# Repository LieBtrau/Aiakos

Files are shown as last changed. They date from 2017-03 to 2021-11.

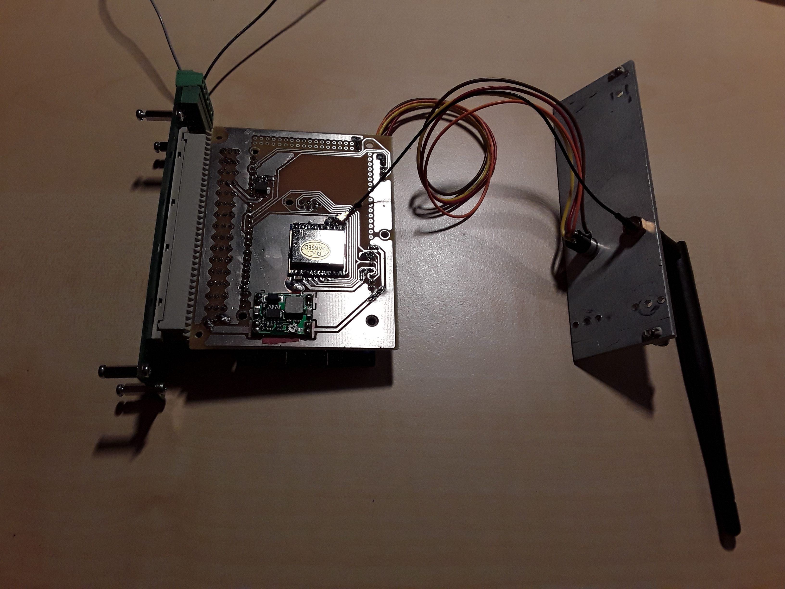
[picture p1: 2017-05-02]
Documentation/Pictures/20170501_215125.jpg

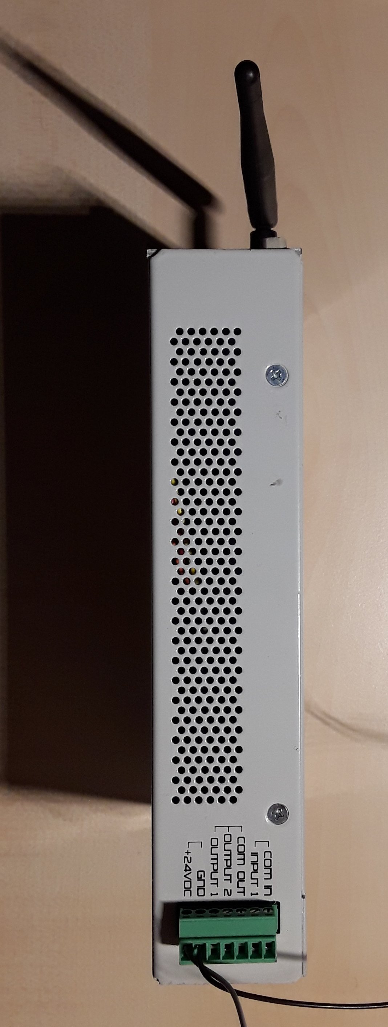
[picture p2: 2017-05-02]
Documentation/Pictures/20170501_215628.jpg

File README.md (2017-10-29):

# This project will solve the following problem
When arriving at home  with my bike, I find the garage door still locked.  I have to stop in front of the closed door, take of my backpack, find the keyfob and activate it.  It takes a few seconds then before the door is fully open and I can enter.  When it's raining heavily, every second outside is a second too much.

# Wish
While riding and coming near to my house, press a button on my bike so that the door opens.  By the time I arrive at the door, it's fully open and I can ride in the garage without having to stop on the drive way.

# Solution
The system will consist of three parts:  

* door controller in the garage  
* BLE-enabled key fob in my back pack  
* Wake up initializer  

## Door controller in the garage
The [door controller](https://github.com/LieBtrau/Aiakos/wiki/Garage-controller) is mounted in the garage and connected to the electric motor that can open and close the door.  With its [LoRa](https://www.lora-alliance.org/) module the controller can securely communicate to the key fob.  To make the system operational, the key fob must be paired with the door controller.  The pairing is done by connecting the door controller to the key fob with an audio-jack cable and pressing the button on the key fob.  The serial connection prevents man-in-the-middle (MITM) attacks.  To prevent eavesdropping, the serial connection is secured using [ECDH](https://en.wikipedia.org/wiki/Elliptic-curve_Diffie%E2%80%93Hellman).

## Key fob 
The [key fob](https://github.com/LieBtrau/Aiakos/wiki/Key-fob) is the access token to the system and should be kept safely by the user.  The key fob's Lora module enables communication to the door controller.  The key fob will be asleep most of the time.  When it receives a valid awake command, it will instruct the door controller to open/close the garage door.  The user can wake the key fob in two ways: either by pushing the key fob button, or by pushing the button on the wake up initializer.  
The key fob incorporates a [Bluetooth Low Energy](https://en.wikipedia.org/wiki/Bluetooth_Low_Energy) module to communicate with the wake up initializer.  The key fob will only allow a paired initializer to wake it up.  Pairing involves connecting the fob to the initializer using an audio jack cable and pressing the key fob button.

## Wake up initializer

# Alternatives
## Smartphone and garage controller with WiFi
An off-the-shelf bluetooth tracker is attached to the bike.  The user has a smartphone with a wireless data connection and bluetooth low energy support.  The garage is equipped with an internet connected controller.  After binding the tracker with the smartphone, the system is ready to use.  
Pressing the button on the bluetooth tracker, wakes up the service running on the smartphone.  The smartphone uses geo-location service to check if the smartphone is in the neighbourhood of the garage.  If so, then a command is sent through WiFi to instruct the garage controller to open the door.  
## Smartphone and garage controller with WiFi
The garage controller can be equipped with a bluetooth low energy peripheral IC.  The user could then operate the door using an application on a smartphone.  

*

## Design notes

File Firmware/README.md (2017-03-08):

#This project will solve the following problem
When arriving at home  with my bike, I find the garage door still locked.  I have to stop in front of the closed door, take of my backpack, find the keyfob and activate it.  It takes a few seconds then before the door is fully open and I can enter.  When it's raining heavily, every second outside is a second too much.

#Wish
While riding and coming near to my house, press a button on my bike so that the door opens.  By the time I arrive at the door, it's fully open and I can ride in the garage without having to stop on the drive way.

#Proposed solutions
##Not implemented: Using smartphone
An off-the-shelf bluetooth tracker is attached to the bike.  The user has a smartphone with a wireless data connection and bluetooth low energy support.  The garage is equipped with an internet connected controller.  After binding the tracker with the smartphone, the system is ready to use.  
Pressing the button on the bluetooth tracker, wakes up the service running on the smartphone.  The smartphone uses geo-location service to check if the smartphone is in the neighbourhood of the garage.  If so, then a command is sent through the cloud to instruct the garage controller to open the door.  

##Without smartphone
The system will consist of three parts:  

* door controller in the garage  
* Wake up initializer
* NFC-enabled key fob in my back pack  

###Door controller in the garage
The door controller in the garage is connected to the motor that can open and close the gate.  It will only do this when an authenticated request from a paired keyfob has been received by its wireless UHF-receiver.
During system setup, the key fob will have to be securely bound to the garage controller.  For ease of use, compliance with future addon, and prevention of man-in-the-middle (MITM) attacks, serial communication will be used.  The user will use a button to put the door controller in learn mode.  To pair the keyfob, the user connects keyfob and the controller with an audio jack cable and that's it.  Audio jack cables and connectors are cheaper and less power hungry than NFC readers and tags.

###Wake up initializer

###Key fob
After the key fob has been paired with the controller in the garage it will return to a low power sleep mode.  Reception of the correct code on the LF-receiver will wake up the key fob.  The UHF-transmitter in the key fob will then automatically send a request to the garage controller to open the gate.

###Used technologies
* 434MHz LoRa wireless communication
* Bluetooth Low Energy
* ...

#Future addon
The garage controller can be equipped with a bluetooth low energy peripheral IC.  The user could then operate the door using an application on a smartphone.  

* [Garage controller](../../wiki/Master:-garage-controller)

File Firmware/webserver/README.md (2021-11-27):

# What is this all about?
It's an ESP32 running a webserver.  Once you typed in the correct pincode on the ESP32's webpage, a GPIO will be toggled, which will open the garagedoor.
## Security
3 layer security:

 1. The ESP32 only exists as a local device on the Wifi-network.  It's behind the firewall, so it can't be accessed from the internet.  You'll need to know the WiFi-password first.
 2. IP-traffic to the ESP32 is encrypted by TLS1.2, using a self-signed certificate
 3. The user must know the correct pin code.
## Implementation
The code is written in Micropython/CircuitPython.  The source files can be found in this repository.  To make it all work, you'll need to generate your own configuration files.  Examples of these two files follow:
### config.json
    {
	    "secure-connection": "true",
	    "hostname": "esp32_wifi",
	    "secure-tcp-port": "443",
	    "unsecure-tcp-port": "80",
	    "ip-address": "192.168.1.254",
	    "netmask": "255.255.255.0",
	    "default-route": "192.168.1.1",
	    "dns": "8.8.8.8",
	    "pincodes": [
	        "1234",
	        "4321"
	    ]
	}
### wifi-credentials.json
    {
    "SSID" : "MyWifiSSID",
    "PASS" : "MySecretWiFiPassword"
	}

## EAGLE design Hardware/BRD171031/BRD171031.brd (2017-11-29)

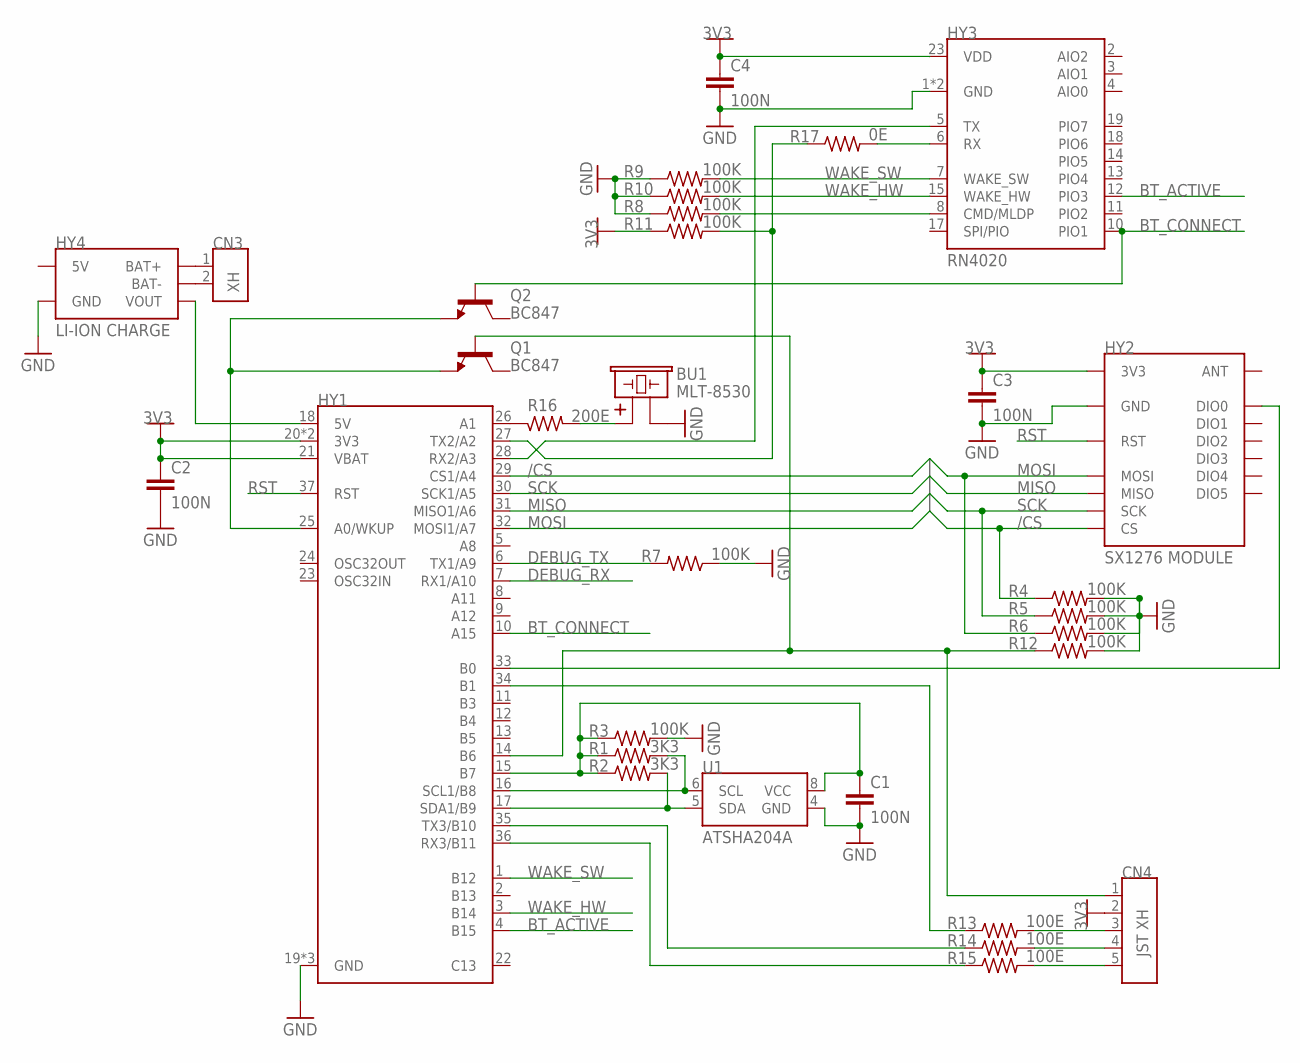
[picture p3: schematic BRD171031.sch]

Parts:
BU1: MLT-8530; BU_8530
C1, C2, C3, C4: 100N; CA_1206
CN3: XH; CN_HDR_1X2_180D_P25_JST_B2B-XH
CN4: JST XH; CN_HDR_1X5_180D_P25_JST_B5B-XH
HY1: HY_DEVBRD_BLUEPILL; HY_DEVBRD_BLUEPILL_SMD
HY2: SX1276 MODULE; HY_SX1276
HY3: RN4020; HY_BLE_RN4020
HY4: LI-ION CHARGE; HY_PMMOD_LIION
Q1, Q2: BC847; SC_SOT23
R1, R2: 3K3; RE_1206
R3, R4, R5, R6, R7, R8, R9, R10, R11, R12: 100K; RE_1206
R13, R14, R15: 100E; RE_1206
R16: 200E; RE_1206
R17: 0E; RE_1206
U1: ATSHA204A; SC_SO08

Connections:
3V3: C2.1, C3.1, C4.1, CN4.2, HY1.20 (3V3), HY1.21 (VBAT), HY1.38 (3V3), HY2.VCC (3V3), HY3.23 (VDD), R11.1
/CS: HY1.29 (CS1/A4), HY2.NSS (CS), R4.1
BTN: CN4.1, HY1.14 (B6), Q1.1 (B), R12.1
BT_ACTIVE: HY1.4 (B15), HY3.12 (PIO3)
BT_CONNECT: HY1.10 (A15), HY3.10 (PIO1), Q2.1 (B)
DEBUG_RX: HY1.7 (RX1/A10)
DEBUG_TX: HY1.6 (TX1/A9), R7.2
GND: BU1.2, C1.2, C2.2, C3.2, C4.2, HY1.19 (GND), HY1.39 (GND), HY1.40 (GND), HY2.GND, HY2.GND@1 (GND), HY2.GND@2 (GND), HY3.1 (GND), HY3.24 (GND), HY4.GND1 (GND), HY4.GND2 (GND), R3.2, R4.2, R5.2, R6.2, R7.1, R8.1, R9.1, R10.1, R12.2, U1.4 (GND)
MISO: HY1.31 (MISO1/A6), HY2.MISO
MOSI: HY1.32 (MOSI1/A7), HY2.MOSI, R6.1
unnamed: HY3.6 (RX), R17.2
unnamed: HY1.33 (B0), HY2.DIO0
unnamed: HY1.27 (TX2/A2), R11.2, R17.1
unnamed: HY1.28 (RX2/A3), HY3.5 (TX)
unnamed: HY3.8 (CMD/MLDP), R8.2
unnamed: HY1.36 (RX3/B11), R15.1
unnamed: HY1.35 (TX3/B10), R14.1
unnamed: HY1.34 (B1), R13.1
unnamed: HY1.25 (A0/WKUP), Q1.2 (E), Q2.2 (E)
unnamed: HY1.26 (A1), R16.1
unnamed: CN4.3, R13.2
unnamed: CN4.4, R14.2
unnamed: CN4.5, R15.2
unnamed: BU1.1, R16.2
unnamed: HY1.18 (5V), HY4.OUT+ (VOUT)
unnamed: CN3.1, HY4.B+ (BAT+)
unnamed: CN3.2, HY4.B- (BAT-)
PWR_U1: C1.1, HY1.15 (B7), R1.1, R2.1, R3.1, U1.8 (VCC)
RST: HY1.37 (RST), HY2.REST (RST)
SCK: HY1.30 (SCK1/A5), HY2.SCK, R5.1
SCL: HY1.16 (SCL1/B8), R1.2, U1.6 (SCL)
SDA: HY1.17 (SDA1/B9), R2.2, U1.5 (SDA)
WAKE_HW: HY1.3 (B14), HY3.15 (WAKE_HW), R10.2
WAKE_SW: HY1.1 (B12), HY3.7 (WAKE_SW), R9.2

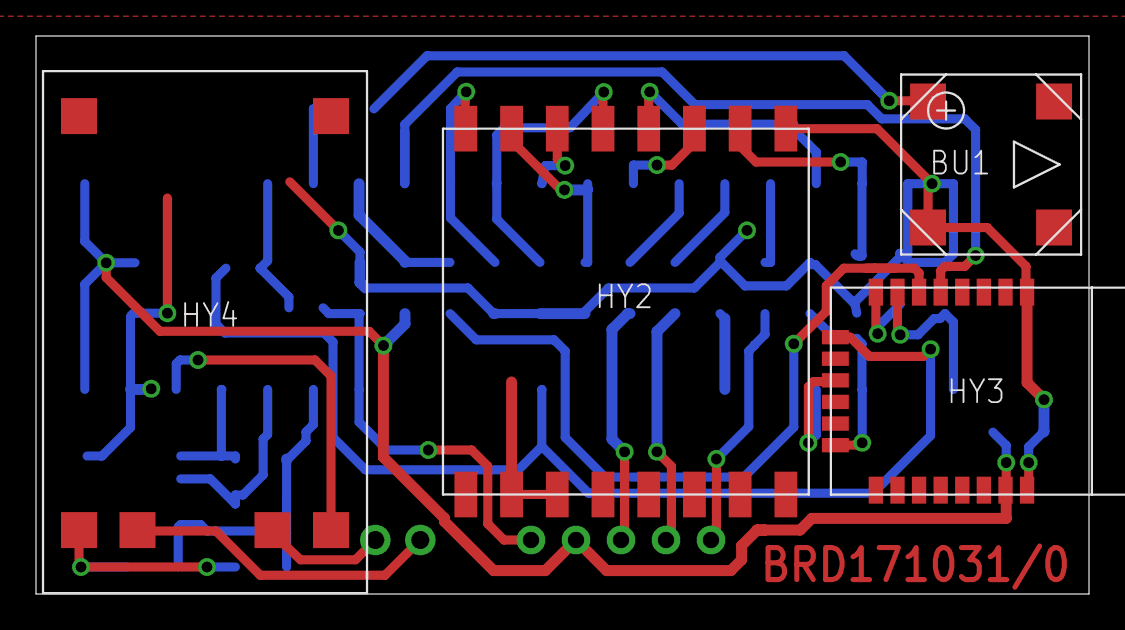
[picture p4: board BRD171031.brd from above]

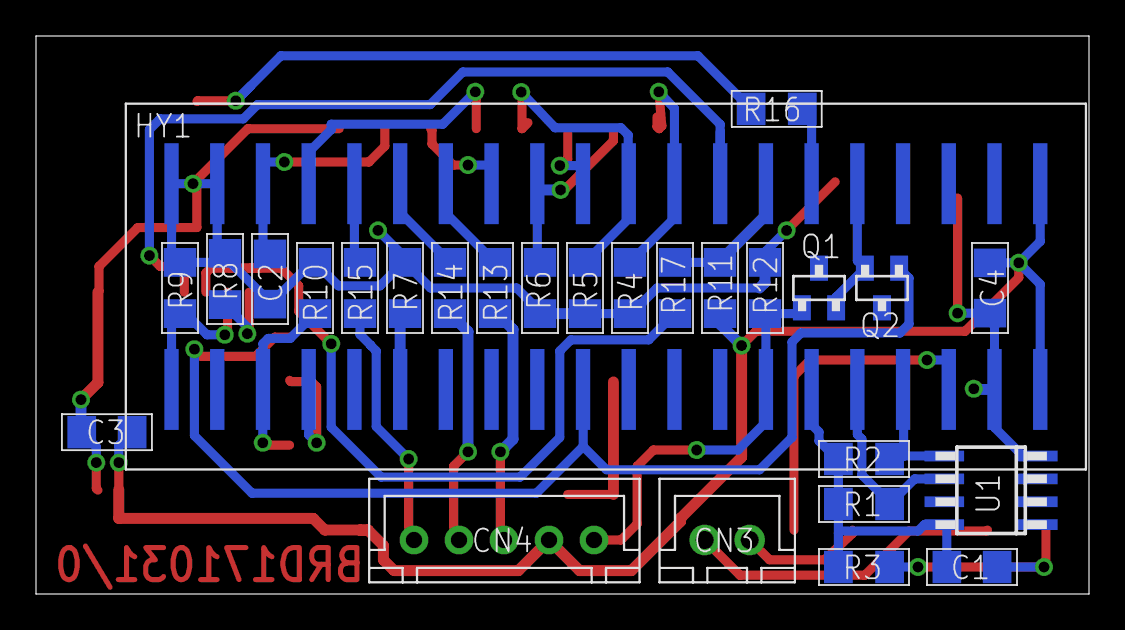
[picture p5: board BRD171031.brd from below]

Board: 2 copper layers, 58.5 x 31.0 mm, 32 parts (27 on the bottom side), 33 nets.

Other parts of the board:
U$2: MC_FRAME_A5

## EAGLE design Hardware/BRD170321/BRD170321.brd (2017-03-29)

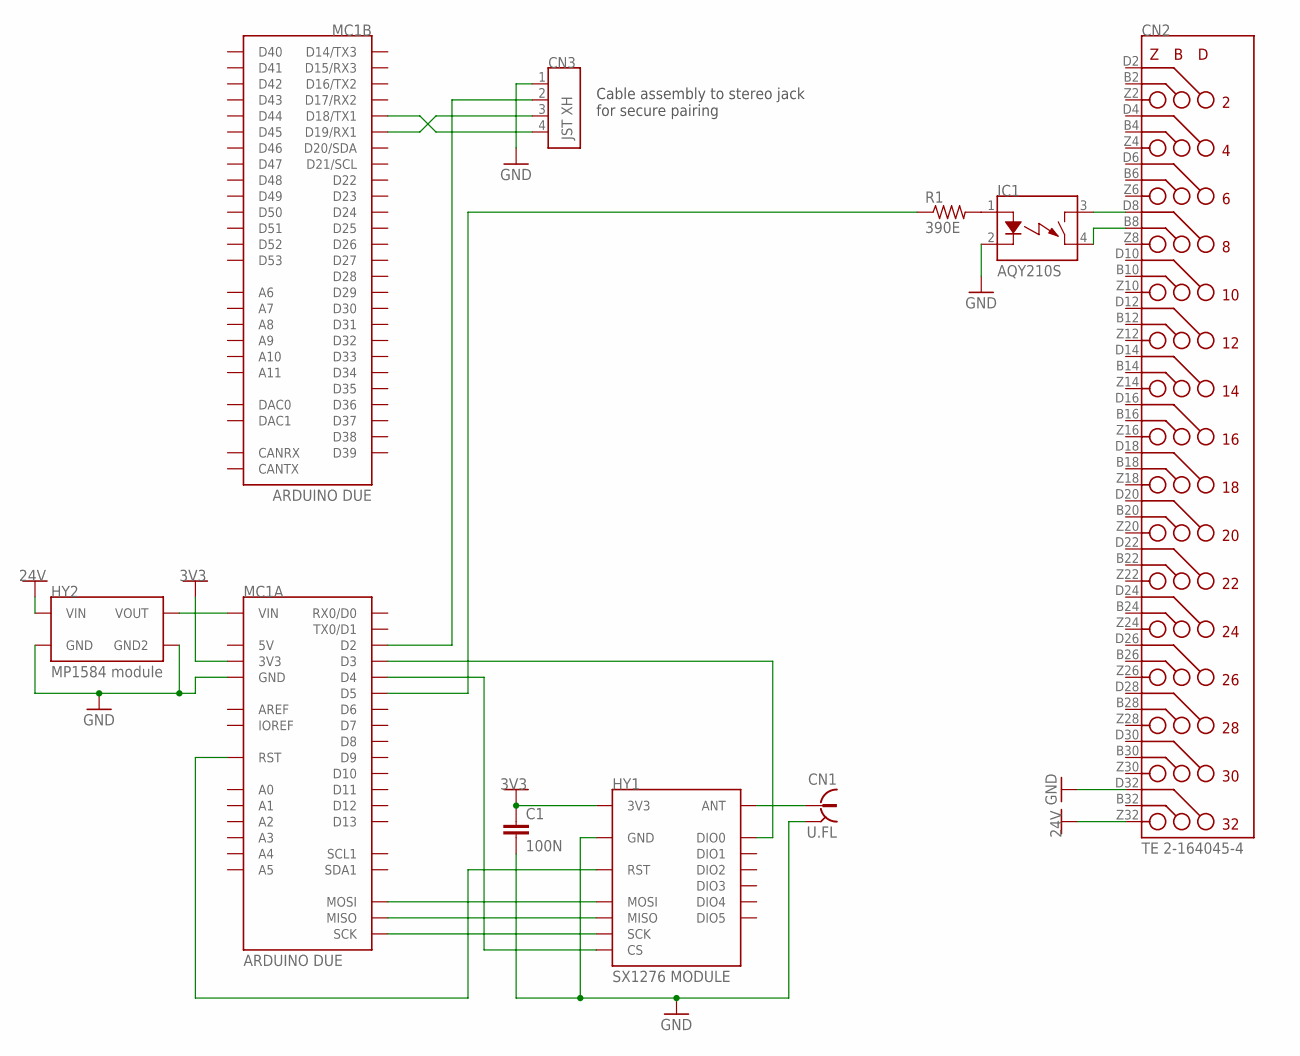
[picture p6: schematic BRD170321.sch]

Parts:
C1: 100N; CA_1206
CN1: U.FL; CN_RF_U.FL_MALE
CN2: TE 2-164045-4; CN_HDR_DIN41612F_90D
CN3: JST XH; CN_HDR_1X4_180D_P25_JST_B4B-XH
HY1: SX1276 MODULE; HY_SX1276
HY2: MP1584 module; HY_MP1584
IC1: AQY210S; SC_SO6_P4
MC1: ARDUINO DUE; MC_ARDUINO_DUE
R1: 390E; RE_1206

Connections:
3V3: C1.1, HY1.VCC (3V3), MC1.3.3V (3V3)
24V: CN2.Z32 (32Z), HY2.IN+ (VIN)
GND: C1.2, CN1.2A (OUTER), CN1.2B (OUTER), CN2.D32 (32D), CN3.1, HY1.GND, HY1.GND@1 (GND), HY1.GND@2 (GND), HY2.IN- (GND), HY2.OUT- (GND2), IC1.2 (C), MC1.GND@1 (GND), MC1.GND@2 (GND), MC1.GND@3 (GND), MC1.GND@4 (GND), MC1.GND@5 (GND), MC1.GND@6 (GND)
unnamed: IC1.1 (A), R1.2
unnamed: CN1.1 (INNER), HY1.ANT
unnamed: HY1.MOSI, MC1.MOSI
unnamed: HY2.OUT+ (VOUT), MC1.VIN
unnamed: CN2.D8 (8D), IC1.3 (D1)
unnamed: CN2.B8 (8B), IC1.4 (D2)
unnamed: MC1.5 (D5), R1.1
unnamed: HY1.MISO, MC1.MISO
unnamed: HY1.SCK, MC1.SCK
unnamed: HY1.NSS (CS), MC1.4 (D4)
unnamed: HY1.DIO0, MC1.3 (D3)
unnamed: HY1.REST (RST), MC1.RESET (RST), MC1.RESET@2 (RST)
unnamed: CN3.2, MC1.2 (D2)
unnamed: CN3.3, MC1.19 (D19/RX1)
unnamed: CN3.4, MC1.18 (D18/TX1)

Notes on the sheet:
Cable assembly to stereo jack for secure pairing

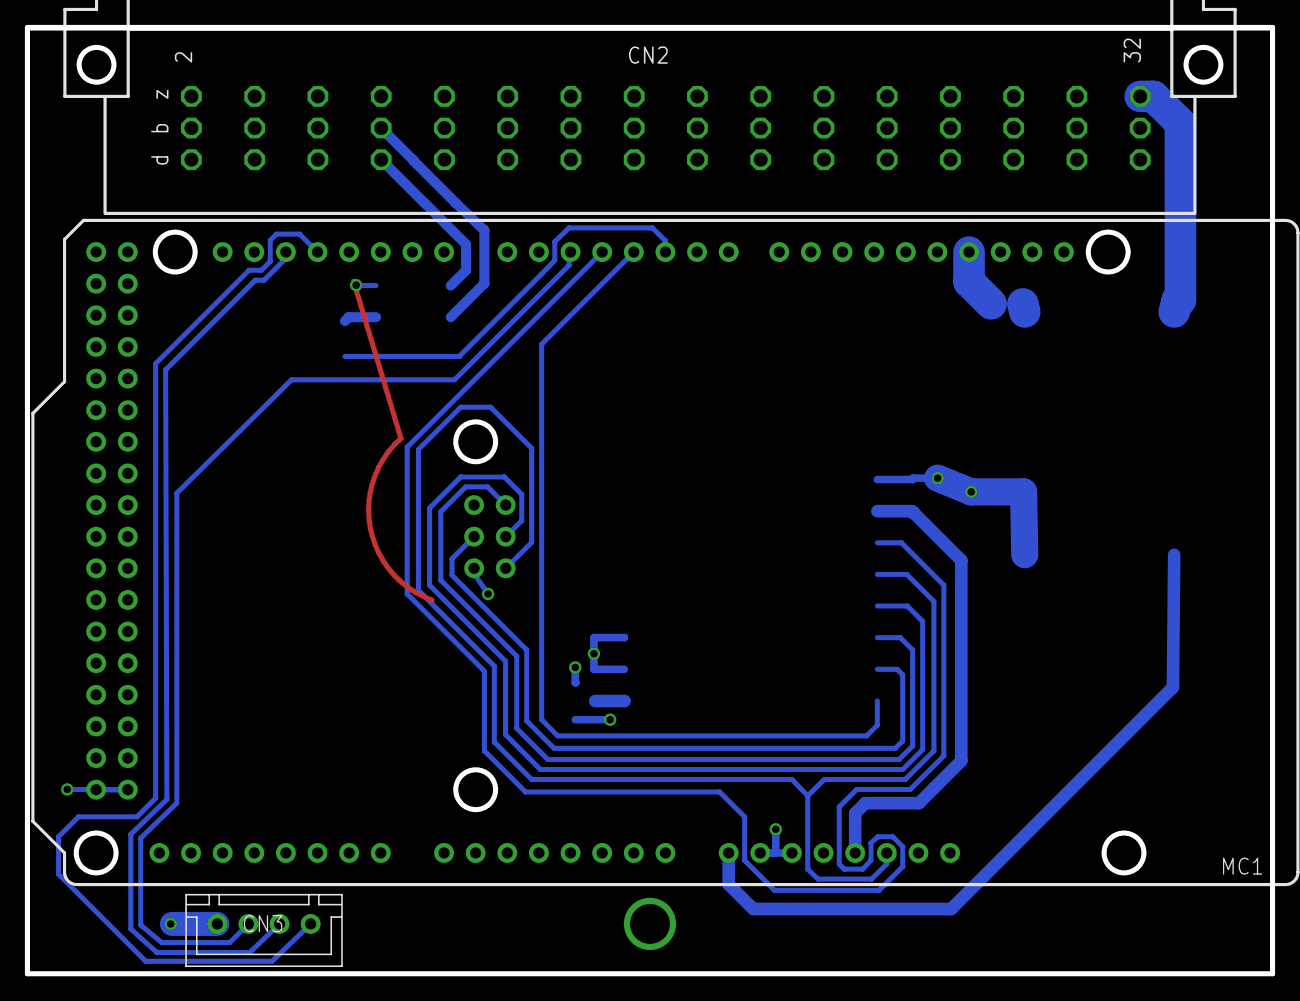
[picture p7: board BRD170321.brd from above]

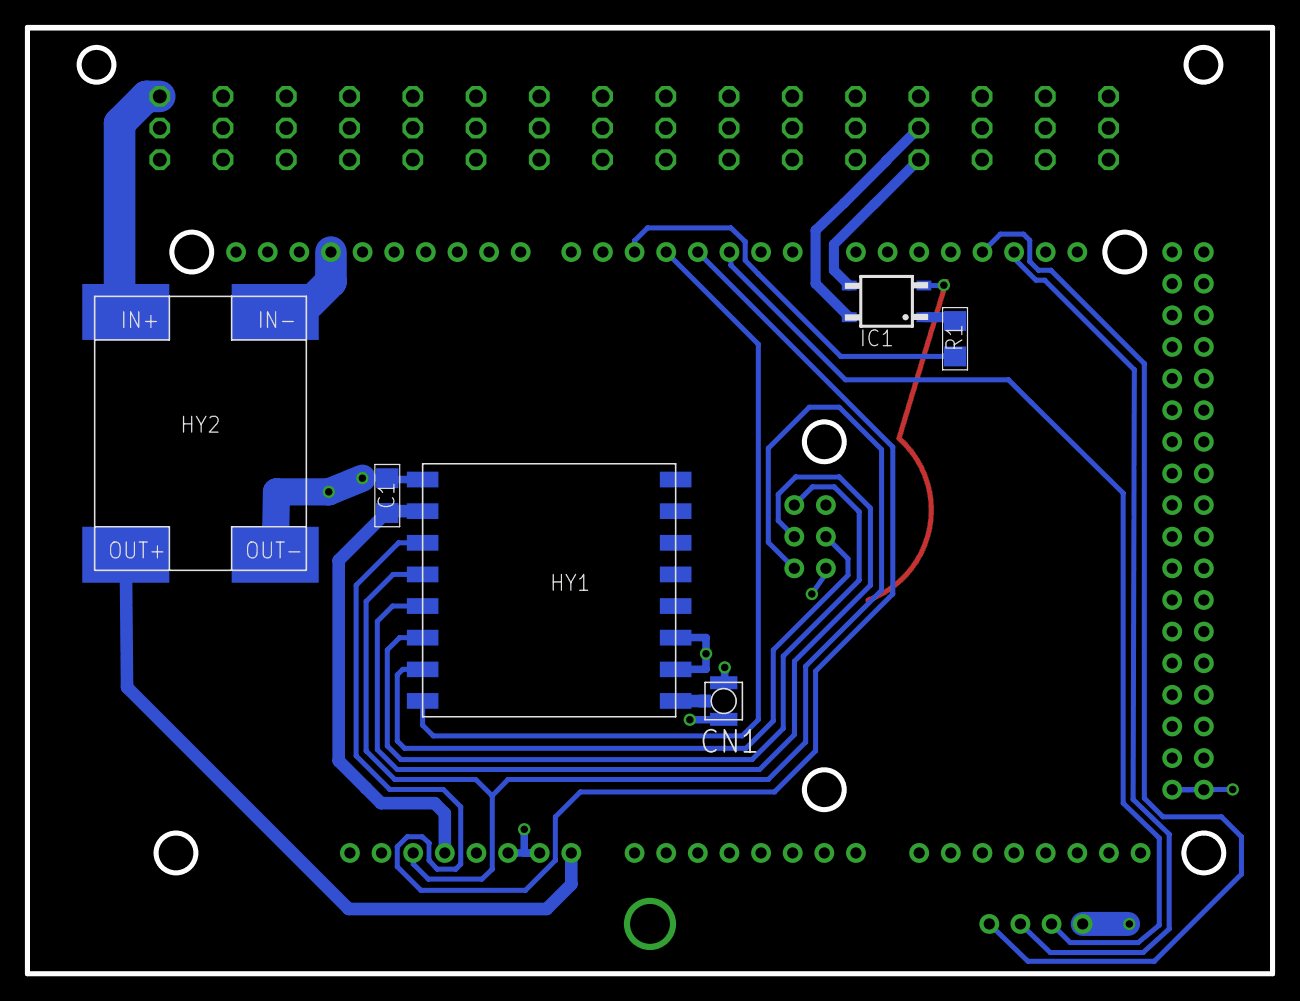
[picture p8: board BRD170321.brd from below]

Board: 2 copper layers, 100.0 x 76.0 mm, 11 parts (6 on the bottom side), 18 nets.

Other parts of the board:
DRILEGEND: DRILEGEND
U$6: MC_FRAME_A5

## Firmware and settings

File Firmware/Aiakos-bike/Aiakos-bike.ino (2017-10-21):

/*Connections between Nucleo and RN4020, on Nucleo Serial2 is connected to the debugger
 * RN4020.1 (GND)       -> GND
 * RN4020.5 (TX)        -> D2 (Serial1_RX)
 * RN4020.6 (RX)        -> D8 (Serial1_TX)
 * RN4020.7 (WAKE_SW)   -> D3
 * RN4020.12 (ACT)      -> D4
 * RN4020.15 (WAKE_HW)  -> D5
 * RN4020.PWREN         -> D6
 * RN4020.23 (3V3)      -> 3V3
 */

#include <RH_Serial.h>          //for wired comm
#include "blepairingcentral.h"
#include "debug.h"
#include "blecontrol.h"
#include <Bounce2.h>            //for switch debouncing

void bleEvent(bleControl::EVENT ev);
bool readDataSer(byte* data, byte& length);
bool writeDataSer(byte* data, byte length);

namespace
{
const byte RFID_KEY_SIZE=5;
const byte CABLE_DETECT_PIN=6;
const byte BUTTON_PIN=25;
byte rfid_key[RFID_KEY_SIZE]={0xAA,0xAB,0xAC,0xAD,0xAE};
RH_Serial rhSerial(Serial2);                    //UART3
RHReliableDatagram mgrSerial(rhSerial, 3);
RHReliableDatagram* pmgrSer;
/* WAKE_SW (7)  ->  3
 * BT_ACTIVE(12)->  4
 * WAKE_HW(15)  ->  5
 * enPwr        ->  7
 */
rn4020 rn(Serial1, 3, 4, 5, 7);                 //UART1, for short range wireless
bleControl ble(&rn);
blePairingCentral blePair(writeDataSer, readDataSer, &ble, RFID_KEY_SIZE);
byte peerAddress;
bool bConnected;
unsigned long buttonTimer=0;
Bounce cableDetect=Bounce();
Bounce pushButton=Bounce();
btCharacteristic ble_char_rfid("f1a87912-5950-479c-a5e5-b6cc81cd0502",        //private service
                          "855b1938-83e2-4889-80b7-ae58fcd0e6ca",        //private characteristic
                          btCharacteristic::WRITE_WOUT_RESP,5,           //properties+length
                          btCharacteristic::ENCR_W);                     //security
btCharacteristic ble_char_ias_alertLevel("1802",                                  //IAS Alert Service
                                "2A06",                                  //Alert Level characteristic
                                btCharacteristic::WRITE_WOUT_RESP, 1,    //properties+length
                                btCharacteristic::NOTHING                //security
                                );
}

void setup()
{
    openDebug(9600);
    rhSerial.serial().begin(2400);
    pmgrSer=&mgrSerial;
    peerAddress=2;                  //keyfob has address 2
    if(!pmgrSer->init())
    {
        debug_println("init failed");
    }
    pinMode(CABLE_DETECT_PIN, INPUT_PULLUP);
    cableDetect.attach(CABLE_DETECT_PIN);
    cableDetect.interval(100); // interval in ms
    pinMode(BUTTON_PIN, INPUT_PULLUP);
    pushButton.attach(BUTTON_PIN);
    pushButton.interval(100); // interval in ms
    ble.setEventListener(bleEvent);
    if(!initBleCentral())
    {
        debug_println("Ble init failed.");
        return;
    }
    debug_print("All ok");
}

// the loop function runs over and over again forever
void loop()
{
    cableDetect.update();
    pushButton.update();
    if(!cableDetect.read())
    {
        //Secure pairing mode
        switch(blePair.loop())
        {
        case BlePairing::AUTHENTICATION_OK:
            debug_println("Securely paired");
            break;
        case BlePairing::NO_AUTHENTICATION:
            pmgrSer->resetDatagram();
            break;
        case BlePairing::AUTHENTICATION_BUSY:
            break;
        }
    }else
    {
        //Keyfob wake up mode
        ble.loop();
        if(pushButton.fell())
        {
            buttonTimer=millis();
        }
        if(pushButton.rose())
        {
            if(millis()-buttonTimer<1000)
            {
                //open door

                if(ble.secureConnect(blePair.getRemoteBleAddress()))
                {
                    if(ble.writeRemoteCharacteristic(&ble_char_rfid, rfid_key,RFID_KEY_SIZE))
                    {
                        debug_println("RFID Value written");
                    }
                    ble.disconnect();
                }
            }
            else
            {
                //find key
                if(ble.secureConnect(blePair.getRemoteBleAddress()))
                {
                    byte array[1]={0xBB};
                    if(ble.writeRemoteCharacteristic(&ble_char_ias_alertLevel, array,1))
                    {
                        debug_println("Alert value written");
                    }
                }
            }
        }
    }
}


bool writeDataSer(byte* data, byte length)
{
    debug_print("Sending serial data...");
    debug_printArray(data, length);
    return pmgrSer->sendtoWait(data, length, peerAddress);
}

bool readDataSer(byte *data, byte& length)
{
    byte from;
    if (!pmgrSer->available())
    {
        return false;
    }
    if(!pmgrSer->recvfromAck(data, &length, &from))
    {
        return false;
    }
    if(from != peerAddress)
    {
        debug_print("Sender doesn't match");
        return false;
    }
    debug_print("Received data: ");debug_printArray(data, length);
    return true;
}

void bleEvent(bleControl::EVENT ev)
{
    switch(ev)
    {
    case bleControl::EV_PASSCODE_GENERATED:
        blePair.eventPasscodeGenerated();
        break;
    case bleControl::EV_CONNECTION_DOWN:
        debug_println("Connection down");
        bConnected=false;
        break;
    case bleControl::EV_CONNECTION_UP:
        debug_println("Connection up");
        bConnected=true;
        break;
    default:
        debug_print("Unknown event: ");
        debug_println(ev, DEC);
        break;
    }
}

bool initBleCentral()
{
    char dataname[20];
    const char BT_NAME_BIKE[]="AiakosBike";
    if(!ble.init(115200))
    {
        debug_println("RN4020 not set up");
        return false;
    }
    if(!ble.getBluetoothDeviceName(dataname))
    {
        return false;
    }
    if(strncmp(dataname,BT_NAME_BIKE, strlen(BT_NAME_BIKE)))
    {
        //Module not yet correctly configured
        if(!ble.programCentral())
        {
            return false;
        }
        if(!ble.setBluetoothDeviceName(BT_NAME_BIKE))
        {
            return false;
        }
    }
    rn.getRemoteHandle(&ble_char_rfid);
    blePair.init(rfid_key);
    return ble.beginCentral();
}

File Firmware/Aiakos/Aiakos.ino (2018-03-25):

#include "loradevice.h"
#include "debug.h"
#ifndef ARDUINO_SAM_DUE
#include "STM32Sleep.h"
#include <RTClock.h>
#endif

/* Hardware Connections
 * **************************************************
 * LoRa module
 * **************************************************
 * XL1276    Protrinket  Due    Nucleo   Blue Pill
 *           3V
 *****************************************************
 * NSS       10          4       A2     PA4
 * MOSI      11          ICSP.4  D11    PA7
 * MISO      12          ICSP.1  D12    PA6
 * SCK       13          ICSP.3  D13    PA5 (Be careful on Nucleo, this is the 6th pin on the left row of the right most pin header connector, not the fifth!)
 * REST      RST         RESET   NRST   R
 * DIO0      3           3       D5     PB0
 * VCC       3V          3.3V    3V     3.3
 * GND       G           GND     GND    G
 *
 *****************************************************
 * ATSHA204A for TRNG and unique serial number (bitbanged-I²C, because Arduino Hardwire I²C buffers are too small)
 *****************************************************
                Blue Pill   Nucleo   ATSHA204A
 *****************************************************
 *              PB9         D3      5 (SDA)
 *              PB8         D4      6 (SCL)
 *
 *****************************************************
 * Serial connection for secure pairing
 *                      Due     Nucleo(Keyfob)  Blue Pill
 *****************************************************
 * Tip                   18     D2(UART1_RX)   PB11 (UART3_RX)
 * Ring1                 19     D8(UART1_TX)   PB10 (UART3_TX)
 * Ring2                 2      D6             PB1
 * Sleeve                GND    GND            G
 * Pushbutton                   25             PB6
 *
 *****************************************************
 * Pulse output for opening/closing garage door
 *****************************************************
 * Pulse                 5
 *
 *****************************************************
 * Tone output on key fob
 *****************************************************
 * Tone                  A1
 *
 * Pairing procedure:
 * ------------------
 * Interconnect the keyfob and the garage controller with the stereo jack cable.  Press the blue button on the Nucleo
 * to start the pairing.
 *
 * Authenticating procedure:
 * -------------------------
 * Disconnect the stereo jack cable from the key fob as well as from the garage controller.  Press the blue button on
 * the Nucleo to initiate authentication.
*/

#ifdef ARDUINO_STM_NUCLEO_F103RB
#define ROLE_KEYFOB
#elif defined(ARDUINO_GENERIC_STM32F103C)
#define ROLE_KEYFOB
#elif defined(ARDUINO_SAM_DUE)
#define ROLE_GARAGE_CONTROLLER
#else
#error No device type defined.
#endif

namespace
{
Configuration cfg;
LoRaDevice* ld;
unsigned long ledTimer;
}

#ifdef ROLE_GARAGE_CONTROLLER

#include "garagecontroller.h"
namespace
{
RH_RF95 rhLoRa(4,3);
RH_Serial rhStereoJack(Serial1);
GarageController device(1, &cfg, &rhLoRa, &rhStereoJack, 2);
const byte pinLED=13;
}

#elif defined(ROLE_KEYFOB)

#include "keyfob.h"
#include "blecontrol.h"
namespace
{
#ifdef ARDUINO_STM_NUCLEO_F103RB
RH_Serial rhStereoJack(Serial1);
RH_RF95 rhLoRa(A2,5);//NSS, DIO0
KeyFob device(2, &cfg, &rhLoRa, &rhStereoJack, 25, 6, &ble);
#elif defined(ARDUINO_GENERIC_STM32F103C)                           //Blue Pill
RH_Serial rhStereoJack(Serial2);                                    //UART3: Serial port for pairing
RH_RF95 rhLoRa(PA4,PB0);                                           //NSS, DIO0 : for long range wireless
/*Connections to BLE RN4020 module
 * |    Blue pill       |   RN4020
 * -----------------------------------------
 * | 3V                 |   23 (VDD)
 * | G                  |   24 (GND)
 * | PA3 (UART2.RX)     |   5 (UART_TX)
 * | PA2 (UART2.TX)     |   6 (UART_RX)
 * | PB12               |   7 (WAKE_SW)
 * | PB15               |   12 (ACTIVE)
 * | PB14               |   15 (WAKE_HW)
 * | PB13               |   /  EN_PWR
 * | PA15               |   10 (CONNECTION_LED)
 */
rn4020 rn(Serial1, PB12, PB15, PB14, PB13, PA15);
bleControl ble(&rn);
KeyFob device(2, &cfg, &rhLoRa, &rhStereoJack, PB6, PB1, &ble, PA1);
RTClock rt(RTCSEL_LSE);
const byte pinLED=PC13; //Active low
#endif
}

#endif

void setup()
{
    ld=&device;
    ld->getInitialPinStates();
//    pinMode(PA8, OUTPUT);
//    digitalWrite(PA8, HIGH);//It takes 463ms to get here
//    delay(100);
    pinMode(pinLED, OUTPUT);
    ledTimer=millis();
    openDebug(9600);
    debug_println("Waking up");
    if(!cfg.init())
    {
        debug_println("Config invalid");
        while(1);
    }
    if(!ld->setup())
    {
        debug_println("Setup failed");
//        while(1);
    }
}

void loop()
{
    ld->loop();
//#ifdef DEBUG
    ledToggle(500);
}

void ledToggle(unsigned long timeOut)
{
    if(millis()>ledTimer+timeOut)
    {
        digitalWrite(pinLED, digitalRead(pinLED) ? 0 : 1);
        ledTimer=millis();
    }
//#endif
}

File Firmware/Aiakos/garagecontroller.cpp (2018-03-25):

#include "garagecontroller.h"

namespace
{
KryptoKnightComm* pk;
Configuration* cfg;
const byte PULSE_PIN=5;
bool slowMcu=false;
}
void dataReceived(byte* data, byte length);
void setSlowMcuSpeed(bool bSlow);

extern void setKeyInfo(byte* remoteId, byte length);


GarageController::GarageController(byte ownAddress,
                                   Configuration* config,
                                   RH_RF95 *prhLora, RH_Serial *prhSerial, byte cableDetectPin): LoRaDevice(ownAddress, prhLora, prhSerial, cableDetectPin)
{
    pk=&k;
    cfg=config;
    setPeerAddress(2);
}

bool GarageController::setup()
{
#ifdef ARDUINO_SAM_DUE
    initRng();
//#ifndef DEBUG
    //See §9.1 Peripheral identifiers of the SAM3X datasheet
    pmc_disable_periph_clk(2);      // real-time clock
    pmc_disable_periph_clk(3);      // real-time timer
    pmc_disable_periph_clk(4);      // watchdog timer
    pmc_disable_periph_clk(6);      // EEFC0  flash ctrl
    pmc_disable_periph_clk(7);      // EEFC1  flash ctrl
    pmc_disable_periph_clk(9);      // SMC_SDRAMC
    pmc_disable_periph_clk(10);     // SDRAMC
    pmc_disable_periph_clk(11);     // PIO A
    pmc_disable_periph_clk(12);     // PIO B
    pmc_disable_periph_clk(14);     // PIO D
    pmc_disable_periph_clk(15);     // PIO E
    pmc_disable_periph_clk(16);     // PIO F
    pmc_disable_periph_clk(18);     // USART1
    pmc_disable_periph_clk(19);     // USART2
    pmc_disable_periph_clk(20);     // USART3
    pmc_disable_periph_clk(21);     // HSMCI (SD/MMC ctrl, N/C)
    pmc_disable_periph_clk(22);     // TWI/I2C bus 0 (i.MX6 controlling)
    pmc_disable_periph_clk(23);     // TWI/I2C bus 1
    pmc_disable_periph_clk(25);     // SPI1
    pmc_disable_periph_clk(26);     // SSC (I2S digital audio, N/C)
    pmc_disable_periph_clk(27);     // timer/counter 0
    pmc_disable_periph_clk(28);     // timer/counter 1
    pmc_disable_periph_clk(29);     // timer/counter 2
    pmc_disable_periph_clk(30);     // timer/counter 3
    pmc_disable_periph_clk(31);     // timer/counter 4
    pmc_disable_periph_clk(32);     // timer/counter 5
    pmc_disable_periph_clk(33);     // timer/counter 6
    pmc_disable_periph_clk(34);     // timer/counter 7
    pmc_disable_periph_clk(35);     // timer/counter 8
    pmc_disable_periph_clk(36);     // PWM
    pmc_disable_periph_clk(37);     // ADC
    pmc_disable_periph_clk(38);     // DAC ctrl
    pmc_disable_periph_clk(39);     // DMA ctrl
    pmc_disable_periph_clk(40);     // USB OTG high-speed ctrl
    pmc_disable_periph_clk(42);     // ethernet MAC - N/C
    pmc_disable_periph_clk(43);     // CAN controller 0
    pmc_disable_periph_clk(44);     // CAN controller 1
//#else
//    debug_println("Debug: No peripherals disabled to save power.");
//#endif    
    setSlowMcuSpeed(true);
#endif
    if(!LoRaDevice::setup())
    {
        return false;
    }
    k.setMessageReceivedHandler(dataReceived);
    k.setKeyRequestHandler(setKeyInfo);
    pinMode(PULSE_PIN, OUTPUT);
    cableDetect.interval(10); // interval in ms
    return true;
}

void GarageController::loop()
{
    cableDetect.update();
    if(!cableDetect.read())
    {
        if(cableDetect.fell())
        {
            //on falling edge of cable detect, all keys must be cleared.
            debug_println("Entering pairing mode");
            setSlowMcuSpeed(false);
            k.reset();
            cfg->removeAllKeys();
        }
        else
        {
            //Secure pairing mode
            if (ecdh.loop() == EcdhComm::AUTHENTICATION_OK)
            {
                debug_println("Securely paired");
                cfg->addKey(ecdh.getRemoteId(), ecdh.getMasterKey());
            }
        }
    }else
    {
        if(cableDetect.rose())
        {
            debug_println("Leaving pairing mode");
        }
        switch(k.loop())
        {
        case KryptoKnightComm::AUTHENTICATION_AS_PEER_OK:
            debug_println("Message received by remote initiator");
            break;
        case KryptoKnightComm::NO_AUTHENTICATION:
            setSlowMcuSpeed(true);
            break;
        case KryptoKnightComm::AUTHENTICATION_BUSY:
            setSlowMcuSpeed(false);
            break;
        }
    }
}

void dataReceived(byte* data, byte length)
{
    debug_println("Event received with the following data:");
    debug_printArray(data, length);
    const byte PORTPULSE[4]={0xFE, 0xDC, 0xBA, 0x98};
    if(!memcmp(data,PORTPULSE,sizeof(PORTPULSE)))
    {
        debug_println("Generating port pulse.");
        digitalWrite(PULSE_PIN, HIGH);
        delay(500);
        digitalWrite(PULSE_PIN, LOW);
    }
}

void setSlowMcuSpeed(bool bSlow)
{
#ifdef ARDUINO_SAM_DUE
#ifndef DEBUG
    if(slowMcu!=bSlow)
    {
        slowMcu=bSlow;
        pmc_set_writeprotect(false);
        pmc_mck_set_prescaler(bSlow ? 96 : 16);   // 2.6 MHz or 84MHz
    }
#else
    if(slowMcu!=bSlow)
    {
        slowMcu=bSlow;
        debug_print("DEBUG: MCU speed throttling disabled: ");debug_println(bSlow ? "down" : "up");
    }
#endif
#endif
}

void setKeyInfo(byte* remoteId, byte length)
{
    debug_println("Remote ID Event received with the following data:");
    debug_printArray(remoteId, length);
    byte* key = cfg->findKey(remoteId, length);
    if(key)
    {
        pk->setRemoteParty(remoteId, length, key);
    }
    else
    {
        debug_println("Key not found in database.");
    }
}

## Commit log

2014-10-06 Adding the Wireless driver
2014-10-21 Adding the ATECC108 library, but it doesn't compile yet. Also some updates to the readme.md file.
    [ecc108_examples.c]
2014-10-25 This firmware is capable of waking up the device.
2014-11-12 Adding readout of serial number of the device, based on EClet code.
2014-11-22 removing Wire2 library (it was only used by ATECC108)
2014-11-24 Adding Wire2 library again. The standard Wire library has too small buffers.
2015-01-04 For sending IrDA, now also use Timer1 (instead of Timer2), so that this whole library needs only one timer.
2015-01-05 Solving bug: a spurious input capture interrupt was generated when switching from sending to receiving.
2015-01-05 Working IrDa "chat"-application (however, no HW-chips used, communication goes using wires)
2015-09-13 NFC reading works with Arduino Due
2015-09-13 Testing Wireless communication
2015-09-15 Enabling NFC and wireless communication simultaneously.
2015-09-17 Removing ST folder because development on STM32 continues in Nucleo folder.
2016-01-03 Build works for Nucleo on Arduino 1.6.5 Build works for Arduino Due on Arduino 1.6.7
2016-09-04 Finding remote devices works
2017-02-08 Authenticated wireless transfer works, kryptoknight implemented.
2017-02-21 Wireless communication doesn't work well.
    [Aiakos.ino]
2017-02-21 version with working wireless communication
2017-02-21 Fixed wireless communication with authentication
    [Aiakos.ino]
2017-03-05 Secure pairing (wired) and authentication (wireless) are both working
2017-03-07 EEPROM implemented. To be tested.
    [configuration.h]
2017-03-09 Implementing crypto functions for Arduino Due Compilation for Due and Nucleo OK, but not tested.
    [configuration.h]
2017-03-17 cryptohelpers implemented and tested with secure pairing and authenticated text
    [configuration.h]
2017-03-19 Findkey instead of findkeyindex
    [configuration.h]
2017-03-19 Cleaning up configuration interface
    [configuration.h]
2017-03-20 Garage controller and key fob have their own loop(). Pairing and authenticating with stereo cable detect works.
2017-03-29 Moving code to "Firmware" folder
    [configuration.h]
2017-03-29 BRD170321 R00.0x
    [BRD170321.brd, BRD170321.sch]
2017-04-03 Reorganizing project
    [configuration.h]
2017-04-23 Working application for garage controller. All functionality implemented. Debugging enabled
    [configuration.h]
2017-04-24 Fixing bug in storage address of default key
    [configuration.h]
2017-04-30 -Disabling peripherals clocks -Switching CPU speeds at runtime
2017-06-29 Adding project for ProTrinket 3V
2017-09-02 bug fix on sscanf adding findMe
    [Aiakos-bike.ino, Aiakos.ino]
2017-09-05 -Functioning pairing between keyfob & bike -Functioning generating of BLE-event with sending & checking RFID key
    [configuration.h]
2017-09-09 Firmware as programmed in installed garage-controller
    [configuration.h]
2017-09-19 Speeding up booting of Blue Pill
    [configuration.h]
2017-09-24 bug fix with sizeof() rfid key size length now depends on a constant
    [configuration.h]
2017-10-10 Fixing GarageController
    [configuration.h]
2017-10-29 Applying low power to the LoRa module and crypto device
2017-10-29 -cleaning up advertizing code -push button now active high (saves an inverter) -push button detection moved to other pin (for low current purposes)
2017-11-29 Pin swaps for easier PCB layout
    [Aiakos.ino]
2017-11-29 Adding keyfob R00.00
    [BRD171031.brd, BRD171031.sch]
2020-09-27 web server on SSL with pin code reading
2020-09-28 web server checks pin code & responds accordingly
